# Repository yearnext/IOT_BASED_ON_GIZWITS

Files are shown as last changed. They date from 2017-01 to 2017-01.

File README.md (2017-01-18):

# 智能家居平台介绍
本平台通过机智云+Zigbee来完成智能家居平台的搭建，用户可通过设备控制元件或使用已绑定设备的安卓手机来完成对设备的控制工作。

## 一、模块功能介绍
### 1.1 智能电灯功能介绍
1. 可通过电灯上的按键或APP来控制电灯的开启和关闭。
2. 可通过电灯上的状态指示灯来观察电灯目前的状态。
3. 可通过电灯上的复位按键或者使用APP来还原电灯的出厂数据。
4. 可通过APP来操作电灯进入倒计时运行模式。
5. 可通过APP来操作电灯进入时间段运行模式。
6. 支持断电保持设定数据。
7. 支持设定插座开启的状态。
8. 能够智能判断用户的下一步操作。

### 1.2 智能插座功能介绍
1. 可通过插座上的按键或APP来控制插座的开启和关闭。
2. 可通过插座上的状态指示灯来观察插座目前的状态。
3. 可通过插座上的复位按键或者使用APP来还原插座的出厂数据。
4. 可通过APP来操作插座进入倒计时运行模式。
5. 可通过APP来操作插座进入时间段运行模式。
6. 支持断电保持设定数据。
7. 支持设定插座开启的状态。
8. 能够智能判断用户的下一步操作。

### 1.3 智能窗帘功能介绍
1. 支持手动开启/关闭窗帘。
2. 可通过APP控制窗帘开启/关闭的状态。
3. 可通过APP来操作窗帘进入倒计时运行模式。
4. 可通过APP来操作窗帘进入时间段运行模式。
5. 支持设定窗帘上电时的状态。
6. 支持窗帘下雨警报，可根据用户的配置实现窗帘自动关闭操作。
7. 支持读取室内的亮度数据。
8. 支持断电保持设定数据。
9. 可通过窗帘上的复位按键或者使用APP来还原窗帘的出厂数据。

### 1.4 室内环境监测器功能介绍
1. 能够读取室内的温湿度数据。

## 二、设备通讯协议介绍
### 2.1 数据格式介绍

|通讯类型|事件序号|数据发送/接收方设备类型|数据发送/接收方MAC地址|命令|数据长度|数据|校验和|
|:-:|:-:|:-:|:-:|:-:|:-:|:-:|:-:|
|1 Byte|1 Byte|1 Byte|8 Byte|1 Byte|1 Byte|18 Byte|1 Byte|

#### 2.1.1 通讯类型
|通讯代号|意义|简写|
|:-:|:-:|:-:|
|0x00|结束此次通讯流程|END_COMM|
|0x01|APP请求与设备通讯|W2D|
|0x02|设备应答APP通讯|W2D_ACK|
|0x03|设备请求与APP通讯|D2W|
|0x04|APP应答设备通讯|D2W_ACK|
|0x05|网关请求与设备通讯|H2S|
|0x06|设备应答网关请求|H2S_ACK|
|0x07|设备请求与网关通讯|S2H|
|0x08|网关应答设备请求|S2H_ACK|
|0x09|校验码错误|ERROR_CODE|

#### 2.1.2 事件序号
等待应答的事件序号应与应答的事件序号保持一致。

#### 2.1.3 设备类型
|设备类型|设备代码|
|:-:|:-:|
|网关|0x00|
|APP|0x00|
|灯|0x01|
|插座|0x02|
|窗帘|0x03|
|温湿度传感器|0x04|

**若数据从APP发向设备(W2D、D2W_ACK通讯类型)，设备类型填写数据接收端的设备类型。**

**若数据从设备发向APP(W2D_ACK、D2W通讯类型)，设备类型填写数据发送方的设备类型。**

**若数据从协调器发向终端(H2S、S2H_ACK通讯类型)，设备类型填写数据接收端的设备类型。**

**若数据从终端发向协调器(H2S_ACK、S2H通讯类型)，设备类型填写数据发送方的设备类型。**

#### 2.1.4 设备MAC地址
设备的MAC地址。

**若数据从APP发向设备(W2D、D2W_ACK通讯类型)，设备类型填写数据接收端的MAC地址。**

**若数据从设备发向APP(W2D_ACK、D2W通讯类型)，设备类型填写数据发送方的MAC地址。**

**若数据从协调器发向终端(H2S、S2H_ACK通讯类型)，设备类型填写数据接收端的MAC地址。**

**若数据从终端发向协调器(H2S_ACK、S2H通讯类型)，设备类型填写数据发送方的MAC地址。**

#### 2.1.5 命令
见设备数据点介绍。

#### 2.1.6 数据长度
数据长度表示数据的具体长度，不能超过最大数据长度。

#### 2.1.7 数据
见设备数据点介绍。

#### 2.1.8 校验和
校验和的计算方式为把数据包从通讯类型为开始按字节求和得出的结果对256求余。

### 2.2 设备命令介绍
#### 2.2.1 设备通用基本命令
|控制命令|控制命令介绍|权限|数据点|数据点大小|参数枚举|
|:-:|:-:|:-:|:-:|:-:|:-:|
|0x00|设备心跳命令|只读|-|-|-|
|0x01|恢复设备出厂设备命令|只读|-|-|-|
|0x02|设备重启|只读|-|-|-|
|0x03|刷新设备时间|只读|-|-|-|
|0x04|读取设备时间数据|只读|时间数据|7 Byte|-|
|-|-|-|时间-年数据(21世纪)|1 Byte|0~99|
|-|-|-|时间-月数据|1 Byte|1~12|
|-|-|-|时间-日数据|1 Byte|1~31|
|-|-|-|时间-星期数据|1 Byte|1~7|
|-|-|-|时间-小时数据|1 Byte|0~23|
|-|-|-|时间-分钟数据|1 Byte|0~59|
|-|-|-|时间-秒钟数据|1 Byte|0~59|
|0x05|写入设备时间数据|只写|时间数据|7 Byte|-|
|-|-|-|时间-年数据(21世纪)|1 Byte|0~99|
|-|-|-|时间-月数据|1 Byte|1~12|
|-|-|-|时间-日数据|1 Byte|1~31|
|-|-|-|时间-星期数据|1 Byte|1~7|
|-|-|-|时间-小时数据|1 Byte|0~23|
|-|-|-|时间-分钟数据|1 Byte|0~59|
|-|-|-|时间-秒钟数据|1 Byte|0~59|

#### 2.2.2 网关命令介绍
|控制命令|控制命令介绍|权限|数据点|数据点大小|参数枚举|
|:-:|:-:|:-:|:-:|:-:|:-:|
|0x10|设备列表变化|只读|设备的数量|1 Byte|0~255|
|0x11|APP通过该命令获取目前设备的数量|只读|设备的数量|1 Byte|0~255|
|0x12|APP通过该命令获取目前设备的信息|只读|读取的设备信息|10 Byte|-|
|-|-|-|设备编号（第x台设备）|1 Byte|0 ~ 255|
|-|-|-|设备类型|1 Byte|见设备类型|
|-|-|-|设备MAC地址|8 Byte|见设备MAC地址|
|0x13|设备列表读取失败|只读|-|-|-|

**APP获取设备信息流程介绍**
1. APP向网关设备请求获取在线设备数量。
2. 网关应答APP在线设备数量。
3. APP向网关发送需要获取设备信息的设备编号。
4. 网关回复APP请求的设备编号的设备信息(如果网关返回读取失败命令则APP应该重新执行获取设备信息流程)。
5. APP依次读完所有设备的设备信息。

**注：当设备列表有变化时，设备会向APP发送设备列表变化命令并等待APP读取设备信息。**

#### 2.2.3 电灯命令介绍
|设备命令|设备命令介绍|权限|数据点|数据点大小|参数枚举|
|:-:|:-:|:-:|:-:|:-:|:-:|
|0x10|灯的亮度|只读|Status|1 Byte|0~100(0为关闭，100为开启)|
|0x11|灯的亮度|只写|Status|1 Byte|0~100(0为关闭，100为开启)|
|0x12|定时器单次运行设置|只读|详见定时器数据类型介绍|详见定时器数据类型介绍|详见定时器数据类型介绍|
|0x13|定时器单次运行设置|只写|详见定时器数据类型介绍|详见定时器数据类型介绍|详见定时器数据类型介绍|
|0x14|定时器重复运行设置|只读|详见定时器数据类型介绍|详见定时器数据类型介绍|详见定时器数据类型介绍|
|0x15|定时器重复运行设置|只写|详见定时器数据类型介绍|详见定时器数据类型介绍|详见定时器数据类型介绍|
|0x16|电灯上电运行模式|只读|Mode|1 Byte|0(上电时电灯状态为关闭状态)|
|-|-|-|-|-|1(上电时电灯状态为上一次掉电前的状态)|
|0x17|电灯上电运行模式|只写|Mode|1 Byte|0(上电时电灯状态为关闭状态)|
|-|-|-|-|-|1(上电时电灯状态为上一次掉电前的状态)|

#### 2.2.4 插座命令介绍
|设备命令|设备命令介绍|权限|数据点|数据点大小|参数枚举|
|:-:|:-:|:-:|:-:|:-:|:-:|
|0x10|插座状态|只读|Status|1 Byte|0~1(0为插座关闭，1为插座开启)|
|0x11|插座状态|只写|Status|1 Byte|0~1(0为插座关闭，1为插座开启)|
|0x12|定时器单次运行设置|只读|详见定时器数据类型介绍|详见定时器数据类型介绍|详见定时器数据类型介绍|
|0x13|定时器单次运行设置|只写|详见定时器数据类型介绍|详见定时器数据类型介绍|详见定时器数据类型介绍|
|0x14|定时器重复运行设置|只读|详见定时器数据类型介绍|详见定时器数据类型介绍|详见定时器数据类型介绍|
|0x15|定时器重复运行设置|只写|详见定时器数据类型介绍|详见定时器数据类型介绍|详见定时器数据类型介绍|
|0x16|消耗电能|只读|读取插座消耗的电能|1 Byte|0~100|
|0x17|插座上电运行模式|只读|Mode|1 Byte|0(上电时插座状态为关闭状态)|
|-|-|-|-|-|1(上电时插座状态为上一次掉电前的状态)|
|0x18|插座上电运行模式|只写|Mode|1 Byte|0(上电时插座状态为关闭状态)|
|-|-|-|-|-|1(上电时插座状态为上一次掉电前的状态)|

#### 2.2.5 窗帘命令介绍
|设备命令|设备命令介绍|权限|数据点|数据点大小|参数枚举|
|:-:|:-:|:-:|:-:|:-:|:-:|
|0x10|读取窗帘当前状态|只读|Status|1 Byte|窗帘当前状态|
|-|-|-|-|-|窗帘初始化状态(0x00)|
|-|-|-|-|-|窗帘正在开启状态(0x01)|
|-|-|-|-|-|窗帘完成开启状态(0x02)|
|-|-|-|-|-|窗帘全部开启状态(0x03)|
|-|-|-|-|-|窗帘正在关闭状态(0x04)|
|-|-|-|-|-|窗帘完成关闭状态(0x05)|
|-|-|-|-|-|窗帘全部关闭状态(0x06)|
|0x11|控制窗帘操作命令|只写|Status|1 Byte|窗帘操作命令|
|-|-|-|-|-|打开窗帘(0x01)|
|-|-|-|-|-|合上窗帘(0x02)|
|0x12|定时器单次运行设置|只读|详见定时器数据类型介绍|详见定时器数据类型介绍|详见定时器数据类型介绍|
|0x13|定时器单次运行设置|只写|详见定时器数据类型介绍|详见定时器数据类型介绍|详见定时器数据类型介绍|
|0x14|定时器重复运行设置|只读|详见定时器数据类型介绍|详见定时器数据类型介绍|详见定时器数据类型介绍|
|0x15|定时器重复运行设置|只写|详见定时器数据类型介绍|详见定时器数据类型介绍|详见定时器数据类型介绍|
|0x16|APP通过该命令读取窗帘的工作模式|只读|智能工作模式开关|1 Byte|0~1|
|-|-|-|设定自动关闭窗帘的亮度|1 Byte|0~100|
|0x17|APP通过该命令设置窗帘的工作模式|只写|智能工作模式开关|1 Byte|0~1|
|-|-|-|设定自动关闭窗帘的亮度|1 Byte|0~100|
|0x18|下雨警报|只读|窗帘向APP发送下雨警报|1 Byte|0~1|
|0x19|窗帘检测到的光照前的强度|只读|窗帘向APP发送下雨警报|1 Byte|0~100|
|0x1A|窗帘上电运行模式|只读|窗帘上电运行状态|1 Byte|-|
|-|-|-|-|-|保持现有状态(0x00)|
|-|-|-|-|-|关闭窗帘(0x01)|
|-|-|-|-|-|开启窗帘(0x02)|
|0x1B|窗帘上电运行模式|只写|窗帘上电运行状态|1 Byte|-|
|-|-|-|-|-|保持现有状态(0x00)|
|-|-|-|-|-|关闭窗帘(0x01)|
|-|-|-|-|-|开启窗帘(0x02)|

#### 2.2.6 温湿度传感器命令介绍
|设备命令|设备命令介绍|权限|数据点|数据点大小|参数介绍|
|:-:|:-:|:-:|:-:|:-:|:-:|
|0x10|上报当前环境温湿度数据|只读|上报的温湿度数据|2 Byte|-|
|-|-|-|TEMP|1 Byte|0~100|
|-|-|-|HUMI|1 Byte|0~100|
|0x11|读取当前环境温湿度数据|只读|读取的温湿度数据|2 Byte|-|
|-|-|-|TEMP|1 Byte|0~100|
|-|-|-|HUMI|1 Byte|0~100|

#### 2.2.7 定时器数据格式介绍
|数据名称|成员|成员介绍|权限|占用内存|参数介绍|
|:-:|:-:|:-:|:-:|:-:|:-:|:-:|
|定时器工作模式|-|-|只读|1 Byte|-|
|-|-|-|-|-|TIMER_SLEEP_MODE（定时器休眠模式） = 0x00|
|-|-|-|-|-|TIMER_DOWNCNT_MODE（定时器倒计时运行模式） = 0x01|
|-|-|-|-|-|TIMER_PERIOD_MODE（定时器时间段运行模式） = 0x02|
|-|-|-|-|-|TIMER_CIRCUL_MODE（定时器重复运行模式） = 0x03|
|自定义工作参数|-|-|读/写|1 Byte|配置定时器自定义运行模式的工作参数|
|-|保留|保留|保留|Bit 0(占用该字节的第0位)|0~1|
|-|monday|周一工作状态|读/写|Bit 1(占用该字节的第1位)|0~1|
|-|tuesday|周二工作状态|读/写|Bit 2(占用该字节的第2位)|0~1|
|-|wednesday|周三工作状态|读/写|Bit 3(占用该字节的第3位)|0~1|
|-|thursday|周四工作状态|读/写|Bit 4(占用该字节的第4位)|0~1|
|-|friday|周五工作状态|读/写|Bit 5(占用该字节的第5位)|0~1|
|-|saturday|周六工作状态|读/写|Bit 6(占用该字节的第6位)|0~1|
|-|sunday|周日工作状态|读/写|Bit 7(占用该字节的第7位)|0~1|
|定时器工作时间|-|-|读/写|4 Byte|配置定时器的启动时间和停止时间|
|-|Start_Hour|启动时间-小时|读/写|1 Byte|0~23|
|-|Start_Minute|启动时间-分钟|读/写|1 Byte|0~59|
|-|Stop_Hour|启动时间-小时|读/写|1 Byte|0~23|
|-|Stop_Minute|停止时间-分钟|读/写|1 Byte|0~59|
|设备控制状态|-|-|读/写|2 Byte|配置定时器启动、停止时的设备状态|
|-|device_start_status|设备在定时器启动时的状态|读/写|1 Byte|根据设备而定|
|-|device_end_status|设备在定时器停止时的状态|读/写|1 Byte|根据设备而定|

##### 2.2.7.1 倒计时模式参数配置
例：倒计时8小时35分钟后关闭

    Timer_Mode = TIMER_DOWNCNT_MODE;
    Start_Hour = Now_Time_Hour;
    Start_Minute = Now_Time_Minute;
    Stop_Hour = 8;
    Start_Minute = 35;
    device_start_status = now_status;
    device_end_status = off_status;

**注：**
**1. 当设定定时器工作在倒计时模式时，定时器工作一次，不会重复运行。**
**2. 定时器工作在倒计时模式时不允许出现倒计时时间大于24小时的情况，请注意检查。**

##### 2.2.7.2 时间段模式参数配置
例：8:50~9:45开启

    Timer_Mode = TIMER_SIGNAL_MODE;
    Start_Hour = 8;
    Start_Minute = 50;
    Stop_Hour = 9;
    Start_Minute = 45;
    device_start_status = start_status;
    device_end_status = end_status;

**注：**
**1. 当设定定时器工作在时间段模式时，定时器工作一次，不会重复运行。**
**2. 定时器工作在时间段模式时不允许出现启动时间大于停止时间的情况，请注意检查。**

##### 2.2.7.3 重复运行模式参数配置
例：每周一、周二、周三8:50~9:45开启

    Timer_Mode = TIMER_CUSTOM_MODE;
    monday = 1;
    tuesday = 1;
    wednesday = 1;
    Start_Hour = 8;
    Start_Minute = 50;
    Stop_Hour = 9;
    Start_Minute = 45;
    device_start_status = start_status;
    device_end_status = end_status;

**注：**
**1. 当设定定时器工作在重复运行模式时，定时器会重复运行。**
**2. 定时器工作在重复运行模式时不允许出现启动时间大于停止时间的情况，请注意检查。**

### 2.3 通讯流程介绍
#### 2.3.1 APP控制/读取设备数据流程介绍
APP向设备发送数据流程：

    APP ——> 云端 ——> WIFI模组 ——> 网关 ——> 设备

由上述流程可知APP发送的数据经过云端、WIFI模组、网关处理之后然后才到数据的，中间可能存在一些延迟，因此当APP发送写入/读取设备的数据命令数据经过网关时，网关会将数据发送给终端设备，发送成功的话会发送一个应答数据给云端表示设备正在处理此次事件，而设备解析完APP发送的命令数据之后会将设备信息通过设备上报的形式发送给云端(设备上报数据时的设备命令类型为只读命令)。

设备上报数据流程：

    设备 ——> 网关 ——> WIFI模组 ——> 云端 ——> APP

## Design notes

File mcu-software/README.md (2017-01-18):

# 设备通讯协议介绍
## 一、数据格式介绍

|通讯类型|事件序号|数据发送/接收方设备类型|数据发送/接收方MAC地址|命令|数据长度|数据|校验和|
|:-:|:-:|:-:|:-:|:-:|:-:|:-:|:-:|
|1 Byte|1 Byte|1 Byte|8 Byte|1 Byte|1 Byte|18 Byte|1 Byte|

### 1.1 通讯类型
|通讯代号|意义|简写|
|:-:|:-:|:-:|
|0x00|结束此次通讯流程|END_COMM|
|0x01|APP请求与设备通讯|W2D|
|0x02|设备应答APP通讯|W2D_ACK|
|0x03|设备请求与APP通讯|D2W|
|0x04|APP应答设备通讯|D2W_ACK|
|0x05|网关请求与设备通讯|H2S|
|0x06|设备应答网关请求|H2S_ACK|
|0x07|设备请求与网关通讯|S2H|
|0x08|网关应答设备请求|S2H_ACK|
|0x09|校验码错误|ERROR_CODE|

### 1.2 事件序号
等待应答的事件序号应与应答的事件序号保持一致。

### 1.3 设备类型
|设备类型|设备代码|
|:-:|:-:|
|网关|0x00|
|APP|0x00|
|灯|0x01|
|插座|0x02|
|窗帘|0x03|
|温湿度传感器|0x04|

**若数据从APP发向设备(W2D、D2W_ACK通讯类型)，设备类型填写数据接收端的设备类型。**

**若数据从设备发向APP(W2D_ACK、D2W通讯类型)，设备类型填写数据发送方的设备类型。**

**若数据从协调器发向终端(H2S、S2H_ACK通讯类型)，设备类型填写数据接收端的设备类型。**

**若数据从终端发向协调器(H2S_ACK、S2H通讯类型)，设备类型填写数据发送方的设备类型。**

### 1.4 设备MAC地址
设备的MAC地址。

**若数据从APP发向设备(W2D、D2W_ACK通讯类型)，设备类型填写数据接收端的MAC地址。**

**若数据从设备发向APP(W2D_ACK、D2W通讯类型)，设备类型填写数据发送方的MAC地址。**

**若数据从协调器发向终端(H2S、S2H_ACK通讯类型)，设备类型填写数据接收端的MAC地址。**

**若数据从终端发向协调器(H2S_ACK、S2H通讯类型)，设备类型填写数据发送方的MAC地址。**

### 1.5 命令
见设备数据点介绍。

### 1.6 数据长度
数据长度表示数据的具体长度，不能超过最大数据长度。

### 1.7 数据
见设备数据点介绍。

### 1.8 校验和
校验和的计算方式为把数据包从通讯类型为开始按字节求和得出的结果对256求余。

## 二、设备命令介绍
### 2.1 设备通用基本命令
|控制命令|控制命令介绍|权限|数据点|数据点大小|参数枚举|
|:-:|:-:|:-:|:-:|:-:|:-:|
|0x00|设备心跳命令|只读|-|-|-|
|0x01|恢复设备出厂设备命令|只读|-|-|-|
|0x02|设备重启|只读|-|-|-|
|0x03|刷新设备时间|只读|-|-|-|
|0x04|读取设备时间数据|只读|时间数据|9 Byte|-|
|-|-|-|时间-秒钟数据|1 Byte|0~59|
|-|-|-|时间-分钟数据|1 Byte|0~59|
|-|-|-|时间-小时数据|1 Byte|0~23|
|-|-|-|时间-日数据|1 Byte|1~31|
|-|-|-|时间-月数据|1 Byte|1~12|
|-|-|-|时间-星期数据|1 Byte|1~7|
|-|-|-|时间-年数据|2 Byte|0~65535|
|-|-|-|数据有效位|1 Byte|1:该数据为有效数据|
|-|-|-|-|-|0:该数据为无效数据|
|0x05|写入设备时间数据|只写|时间数据|9 Byte|-|
|-|-|-|时间-秒钟数据|1 Byte|0~59|
|-|-|-|时间-分钟数据|1 Byte|0~59|
|-|-|-|时间-小时数据|1 Byte|0~23|
|-|-|-|时间-日数据|1 Byte|1~31|
|-|-|-|时间-月数据|1 Byte|1~12|
|-|-|-|时间-星期数据|1 Byte|1~7|
|-|-|-|时间-年数据|2 Byte|0~65535|
|-|-|-|数据有效位|1 Byte|1:该数据为有效数据|
|-|-|-|-|-|0:该数据为无效数据|

### 2.2 网关命令介绍
|控制命令|控制命令介绍|权限|数据点|数据点大小|参数枚举|
|:-:|:-:|:-:|:-:|:-:|:-:|
|0x10|设备列表变化|只读|设备的数量|1 Byte|0~255|
|0x11|APP通过该命令获取目前设备的数量|只读|设备的数量|1 Byte|0~255|
|0x12|APP通过该命令获取目前设备的信息|只读|读取的设备信息|10 Byte|-|
|-|-|-|设备编号（第x台设备）|1 Byte|0 ~ 255|
|-|-|-|设备类型|1 Byte|见设备类型|
|-|-|-|设备MAC地址|8 Byte|见设备MAC地址|
|0x13|设备列表读取失败|只读|-|-|-|

**APP获取设备信息流程介绍**
1. APP向网关设备请求获取在线设备数量。
2. 网关应答APP在线设备数量。
3. APP向网关发送需要获取设备信息的设备编号。
4. 网关回复APP请求的设备编号的设备信息(如果网关返回读取失败命令则APP应该重新执行获取设备信息流程)。
5. APP依次读完所有设备的设备信息。

**注：当设备列表有变化时，设备会向APP发送设备列表变化命令并等待APP读取设备信息。**

### 2.3 电灯命令介绍
|设备命令|设备命令介绍|权限|数据点|数据点大小|参数枚举|
|:-:|:-:|:-:|:-:|:-:|:-:|
|0x10|灯的亮度|只读|Status|1 Byte|0~100(0为关闭，100为开启)|
|0x11|灯的亮度|只写|Status|1 Byte|0~100(0为关闭，100为开启)|
|0x12|定时器单次运行设置|只读|详见定时器数据类型介绍|详见定时器数据类型介绍|详见定时器数据类型介绍|
|0x13|定时器单次运行设置|只写|详见定时器数据类型介绍|详见定时器数据类型介绍|详见定时器数据类型介绍|
|0x14|定时器重复运行设置|只读|详见定时器数据类型介绍|详见定时器数据类型介绍|详见定时器数据类型介绍|
|0x15|定时器重复运行设置|只写|详见定时器数据类型介绍|详见定时器数据类型介绍|详见定时器数据类型介绍|
|0x16|电灯上电运行模式|只读|Mode|1 Byte|0(上电时电灯状态为关闭状态)|
|-|-|-|-|-|1(上电时电灯状态为上一次掉电前的状态)|
|0x17|电灯上电运行模式|只写|Mode|1 Byte|0(上电时电灯状态为关闭状态)|
|-|-|-|-|-|1(上电时电灯状态为上一次掉电前的状态)|

### 2.4 插座命令介绍
|设备命令|设备命令介绍|权限|数据点|数据点大小|参数枚举|
|:-:|:-:|:-:|:-:|:-:|:-:|
|0x10|插座状态|只读|Status|1 Byte|0~1(0为插座关闭，1为插座开启)|
|0x11|插座状态|只写|Status|1 Byte|0~1(0为插座关闭，1为插座开启)|
|0x12|定时器单次运行设置|只读|详见定时器数据类型介绍|详见定时器数据类型介绍|详见定时器数据类型介绍|
|0x13|定时器单次运行设置|只写|详见定时器数据类型介绍|详见定时器数据类型介绍|详见定时器数据类型介绍|
|0x14|定时器重复运行设置|只读|详见定时器数据类型介绍|详见定时器数据类型介绍|详见定时器数据类型介绍|
|0x15|定时器重复运行设置|只写|详见定时器数据类型介绍|详见定时器数据类型介绍|详见定时器数据类型介绍|
|0x16|消耗电能|只读|读取插座消耗的电能|1 Byte|0~100|
|0x17|插座上电运行模式|只读|Mode|1 Byte|0(上电时插座状态为关闭状态)|
|-|-|-|-|-|1(上电时插座状态为上一次掉电前的状态)|
|0x18|插座上电运行模式|只写|Mode|1 Byte|0(上电时插座状态为关闭状态)|
|-|-|-|-|-|1(上电时插座状态为上一次掉电前的状态)|

### 2.5 窗帘命令介绍
|设备命令|设备命令介绍|权限|数据点|数据点大小|参数枚举|
|:-:|:-:|:-:|:-:|:-:|:-:|
|0x10|读取窗帘当前状态|只读|Status|1 Byte|窗帘当前状态|
|-|-|-|-|-|窗帘初始化状态(0x00)|
|-|-|-|-|-|窗帘正在开启状态(0x01)|
|-|-|-|-|-|窗帘完成开启状态(0x02)|
|-|-|-|-|-|窗帘全部开启状态(0x03)|
|-|-|-|-|-|窗帘正在关闭状态(0x04)|
|-|-|-|-|-|窗帘完成关闭状态(0x05)|
|-|-|-|-|-|窗帘全部关闭状态(0x06)|
|0x11|控制窗帘操作命令|只写|Status|1 Byte|窗帘操作命令|
|-|-|-|-|-|窗帘动作停止(0x00)|
|-|-|-|-|-|开启窗帘(0x01)|
|-|-|-|-|-|关闭窗帘(0x02)|
|0x12|定时器单次运行设置|只读|详见定时器数据类型介绍|详见定时器数据类型介绍|详见定时器数据类型介绍|
|0x13|定时器单次运行设置|只写|详见定时器数据类型介绍|详见定时器数据类型介绍|详见定时器数据类型介绍|
|0x14|定时器重复运行设置|只读|详见定时器数据类型介绍|详见定时器数据类型介绍|详见定时器数据类型介绍|
|0x15|定时器重复运行设置|只写|详见定时器数据类型介绍|详见定时器数据类型介绍|详见定时器数据类型介绍|
|0x16|APP通过该命令读取窗帘的工作模式|只读|智能工作模式开关|1 Byte|0~1|
|-|-|-|设定自动关闭窗帘的亮度|1 Byte|0~100|
|0x17|APP通过该命令设置窗帘的工作模式|只写|智能工作模式开关|1 Byte|0~1|
|-|-|-|设定自动关闭窗帘的亮度|1 Byte|0~100|
|0x18|下雨警报|只读|窗帘向APP发送下雨警报|1 Byte|0~1|
|0x19|窗帘检测到的光照前的强度|只读|窗帘检测到的亮度信息|1 Byte|0~100|
|0x1A|窗帘上电运行模式|只读|窗帘上电运行状态|1 Byte|-|
|-|-|-|-|-|保持现有状态(0x00)|
|-|-|-|-|-|关闭窗帘(0x01)|
|-|-|-|-|-|开启窗帘(0x02)|
|0x1B|窗帘上电运行模式|只写|窗帘上电运行状态|1 Byte|-|
|-|-|-|-|-|保持现有状态(0x00)|
|-|-|-|-|-|关闭窗帘(0x01)|
|-|-|-|-|-|开启窗帘(0x02)|

### 2.6 温湿度传感器命令介绍
|设备命令|设备命令介绍|权限|数据点|数据点大小|参数介绍|
|:-:|:-:|:-:|:-:|:-:|:-:|
|0x10|上报当前环境温湿度数据|只读|上报的温湿度数据|2 Byte|-|
|-|-|-|TEMP|1 Byte|0~50|
|-|-|-|HUMI|1 Byte|0~100|
|0x11|读取当前环境温湿度数据|只读|读取的温湿度数据|2 Byte|-|
|-|-|-|TEMP|1 Byte|0~50|
|-|-|-|HUMI|1 Byte|0~100|
注：由于温湿度传感器精度问题，只能检测到0~50摄氏度的温度且温度误差在正负2摄氏度内，检测到的湿度范围为20%~90%，且湿度误差在正负5%范围内。

### 2.7 定时器数据格式介绍
|数据名称|成员|成员介绍|权限|占用内存|参数介绍|
|:-:|:-:|:-:|:-:|:-:|:-:|:-:|
|定时器工作模式|-|-|只读|1 Byte|-|
|-|-|-|-|-|TIMER_SLEEP_MODE（定时器休眠模式） = 0x00|
|-|-|-|-|-|TIMER_DOWNCNT_MODE（定时器倒计时运行模式） = 0x01|
|-|-|-|-|-|TIMER_PERIOD_MODE（定时器时间段运行模式） = 0x02|
|-|-|-|-|-|TIMER_CIRCUL_MODE（定时器重复运行模式） = 0x03|
|自定义工作参数|-|-|读/写|1 Byte|配置定时器自定义运行模式的工作参数|
|-|保留|保留|保留|Bit 0(占用该字节的第0位)|0~1|
|-|monday|周一工作状态|读/写|Bit 1(占用该字节的第1位)|0~1|
|-|tuesday|周二工作状态|读/写|Bit 2(占用该字节的第2位)|0~1|
|-|wednesday|周三工作状态|读/写|Bit 3(占用该字节的第3位)|0~1|
|-|thursday|周四工作状态|读/写|Bit 4(占用该字节的第4位)|0~1|
|-|friday|周五工作状态|读/写|Bit 5(占用该字节的第5位)|0~1|
|-|saturday|周六工作状态|读/写|Bit 6(占用该字节的第6位)|0~1|
|-|sunday|周日工作状态|读/写|Bit 7(占用该字节的第7位)|0~1|
|定时器工作时间|-|-|读/写|4 Byte|配置定时器的启动时间和停止时间|
|-|Start_Hour|启动时间-小时|读/写|1 Byte|0~23|
|-|Start_Minute|启动时间-分钟|读/写|1 Byte|0~59|
|-|Stop_Hour|启动时间-小时|读/写|1 Byte|0~23|
|-|Stop_Minute|停止时间-分钟|读/写|1 Byte|0~59|
|设备控制状态|-|-|读/写|2 Byte|配置定时器启动、停止时的设备状态|
|-|device_start_status|设备在定时器启动时的状态|读/写|1 Byte|根据设备而定|
|-|device_end_status|设备在定时器停止时的状态|读/写|1 Byte|根据设备而定|

#### 2.7.1 倒计时模式参数配置
例：倒计时8小时35分钟后关闭

    Timer_Mode = TIMER_DOWNCNT_MODE;
    Start_Hour = Now_Time_Hour;
    Start_Minute = Now_Time_Minute;
    Stop_Hour = 8;
    Start_Minute = 35;
    device_start_status = now_status;
    device_end_status = off_status;

**注：**
**1. 当设定定时器工作在倒计时模式时，定时器工作一次，不会重复运行。**
**2. 定时器工作在倒计时模式时不允许出现倒计时时间大于24小时的情况，请注意检查。**

#### 2.7.2 时间段模式参数配置
例：8:50~9:45开启

    Timer_Mode = TIMER_SIGNAL_MODE;
    Start_Hour = 8;
    Start_Minute = 50;
    Stop_Hour = 9;
    Start_Minute = 45;
    device_start_status = start_status;
    device_end_status = end_status;

**注：**
**1. 当设定定时器工作在时间段模式时，定时器工作一次，不会重复运行。**
**2. 定时器工作在时间段模式时不允许出现启动时间大于停止时间的情况，请注意检查。**

#### 2.7.3 重复运行模式参数配置
例：每周一、周二、周三8:50~9:45开启

    Timer_Mode = TIMER_CUSTOM_MODE;
    monday = 1;
    tuesday = 1;
    wednesday = 1;
    Start_Hour = 8;
    Start_Minute = 50;
    Stop_Hour = 9;
    Start_Minute = 45;
    device_start_status = start_status;
    device_end_status = end_status;

**注：**
**1. 当设定定时器工作在重复运行模式时，定时器会重复运行。**
**2. 定时器工作在重复运行模式时不允许出现启动时间大于停止时间的情况，请注意检查。**
>>>>>>> ec588fe... 修复了温湿度数据读取失败的BUG

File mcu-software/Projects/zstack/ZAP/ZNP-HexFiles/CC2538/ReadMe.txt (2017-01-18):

When using ZNP hex images, the host processor must register for specific ZDO
callbacks of interest using the ZDO_MSG_CB_REGISTER API, and will be notified
of the response via the ZDO_MSG_CB_INCOMING command. The ZAP applications
incuded with this release demonstrate this method of handling ZDO responses.

For use with SPI serial interface -
 CC2538ZNP-SPI-Pro.hex -
  To be used with ZNP applications that do not use security.

 CC2538ZNP-SPI-Pro-Secure_Standard.hex -
  To be used with ZNP applications that use standard ZigBee security joining
  where the NWK key is sent in the clear or is pre-configured.

 CC2538ZNP-SPI-Pro-Secure_LinkKeyJoin.hex -
  To be used with ZNP applications that use the Pre-configured Trust Center
  Link Key method of joining where the pre-configured trust center link key
  is used to encrypt the APS tunnel command which contains the NWK key.

For use with UART serial interface -
 CC2538ZNP-UART-Pro.hex -
  To be used with ZNP applications that do not use security.

 CC2538ZNP-UART-Pro-Secure_Standard.hex -
  To be used with ZNP applications that use standard ZigBee security joining
  where the NWK key is sent in the clear or is pre-configured.

 CC2538ZNP-UART-Pro-Secure_LinkKeyJoin.hex -
  To be used with ZNP applications that use the Pre-configured Trust Center
  Link Key method of joining where the pre-configured trust center link key
  is used to encrypt the APS tunnel command which contains the NWK key.

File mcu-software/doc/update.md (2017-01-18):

# IOT_BASE_ON_GIZWITS更新日志——mcu_software_debug分支
## 一、更新日志
**固件版本：IOTBaseOnGizwits_MCUSoftwareDebug_0.2.17_alpha_201612282310**
+ 添加检测到新设备就向APP发送请求更新设备列表命令(待测试)。

**固件版本：IOTBaseOnGizwits_MCUSoftwareDebug_0.2.16_alpha_201612271448**
+ 修改网络时间推送策略，改为网关获取到时间更新主动推送给其他设备，设备会在30s内主动获取网络时间。
+ 添加发送广播程序。
+ 添加写入设备时间命令的解析。

**固件版本：IOTBaseOnGizwits_MCUSoftwareDebug_0.2.15_alpha_201612261700**
+ 添加网关获取网络事时间前置标志。

**固件版本：IOTBaseOnGizwits_MCUSoftwareDebug_0.2.14_alpha_201612261423**
+ 修改窗帘速度检测时间。

**固件版本：IOTBaseOnGizwits_MCUSoftwareDebug_0.2.13_alpha_201612252343**
+ 切换电灯控制按键为电容按键。

**固件版本：IOTBaseOnGizwits_MCUSoftwareDebug_0.2.12_alpha_201612252330**
+ 修复了窗帘定时器回调存在递归的BUG。
+ 修改通讯协议标注错误的问题。

**固件版本：IOTBaseOnGizwits_MCUSoftwareDebug_0.2.11_alpha_201612242230**
+ 修复了定时器运行错误的BUG。
+ 修复了网关获取网络时间过长的BUG。
+ 修改网关清除僵尸设备的时间。
+ 延长设备心跳时间。
+ 添加定时器操作设备的状态上报操作。
+ 修复的下雨状态检测不正常的BUG。
+ 修复通讯协议部分内容。
+ 添加电灯设备的路由分支。
+ 解决了定时器无法在启动后立即停止设备的BUG。

**固件版本：IOTBaseOnGizwits_MCUSoftwareDebug_0.2.10_alpha_201612240022**
+ 修复了电动窗帘上电自动运行的BUG。
+ 修复了电动窗帘按键失灵的BUG。
+ 修复了按键过于灵敏的BUG。

**固件版本：IOTBaseOnGizwits_MCUSoftwareDebug_0.2.9_alpha_201612212337**
+ 完成ZSTACK的NV操作调试。
+ 添加更新日志。
+ 添加设备时钟芯片使能/禁用开关。
+ 添加设备数据保存使能/禁用开关。
+ 修改电灯默认上电状态为关闭状态。
+ 解决了电动窗帘无法实现远程和按键连续控制的BUG。

**固件版本：IOTBaseOnGizwits_MCUSoftwareDebug_0.2.8_alpha_201612201138**
+ 修复倒计时定时器不能正常工作的BUG。

**固件版本：IOTBaseOnGizwits_MCUSoftwareDebug_0.2.7_alpha_201612192312**
+ 修复设备从网关获取时间不正确的BUG。
+ 修复了读取设备列表不正确的BUG。
+ 禁用除COORD设备的串口2驱动。
+ 修改工程清理的批处理文件。
+ 修复设备无法上报消息的BUG。

**固件版本：IOTBaseOnGizwits_MCUSoftwareDebug_0.2.6_alpha_201612181939**
+ 进入DEBUG阶段。

**固件版本：IOTBaseOnGizwits_MCUSoftwareDebug_0.2.5_alpha_201612172346**
+ 解决电动窗帘电机运行时单片机死机的BUG。

**固件版本：IOTBaseOnGizwits_MCUSoftwareDebug_0.2.4_alpha_201612162350**
+ 发现BUG：电动窗帘电机运行时单片机死机。

**固件版本：IOTBaseOnGizwits_MCUSoftwareDebug_0.2.3_alpha_201612142327**
+ 修复zigbee设备底层通讯错误的BUG。
+ 准备进入DEBUG阶段。

**固件版本：IOTBaseOnGizwits_MCUSoftwareDebug_0.2.2_alpha_201612132303**
+ 重写设备列表服务。
+ 分离COORD组件。
+ 增加COORD设备控制程序。
+ 修改空应答机制。
+ 解决抓包失败导致接收缓冲区错误的BUG。
+ 发现：按键反应迟钝BUG。
+ 提高通讯稳定性。

**固件版本：IOTBaseOnGizwits_MCUSoftwareDebug_0.2.1_alpha_201612121622**
+ 修改设备类型判断代码。
+ 使用标准库进行结构体偏移量的计算。
+ 新建工程模版。

**固件版本：IOTBaseOnGizwits_MCUSoftwareDebug_0.2.0_alpha_201612102211**
+ 重写MYPROTOCOL程序框架。

**固件版本：IOTBaseOnGizwits_MCUSoftwareDebug_0.1.27_alpha_201612072222**
+ 修复温湿度数据读取错误的BUG。
+ 降低温湿度数据的读取时间。

**固件版本：IOTBaseOnGizwits_MCUSoftwareDebug_0.1.26_alpha_201612062254**
+ 添加智能插座初始化程序。
+ 修改工程目录结构。

**固件版本：IOTBaseOnGizwits_MCUSoftwareDebug_0.1.25_alpha_201612022237**
+ 添加自动校时服务。

**固件版本：IOTBaseOnGizwits_MCUSoftwareDebug_0.1.24_alpha_201611282112**
+ 添加电动窗帘应答服务。

**固件版本：IOTBaseOnGizwits_MCUSoftwareDebug_0.1.23_alpha_201611271452**
+ 修改电动窗帘模块功能，添加对环境亮度的检测。

**固件版本：IOTBaseOnGizwits_MCUSoftwareDebug_0.1.22_alpha_201611252216**
+ 添加ADC转换程序。
+ 修改定时器组件。

**固件版本：IOTBaseOnGizwits_MCUSoftwareDebug_0.1.21_alpha_201611242229**
+ 修改硬件电路。
+ 完善电动窗帘的硬件抽象层。
+ 修改DS1302驱动程序。

**固件版本：IOTBaseOnGizwits_MCUSoftwareDebug_0.1.20_alpha_201611222241**
+ 修改数据存储服务。

**固件版本：IOTBaseOnGizwits_MCUSoftwareDebug_0.1.19_alpha_201611212228**
+ 修改硬件IO配置。
+ 修改电动窗帘的按键检测处理策略。
+ 修改MYPROTOCOL底层通讯程序。
+ 增加帮助文档。
+ 添加星期计算程序。
+ 完善获取网络时间服务。

**固件版本：IOTBaseOnGizwits_MCUSoftwareDebug_0.1.18_alpha_201611202354**
+ 整合硬件资源。
+ 完善MYPROTOCOL框架。
+ 添加电动窗帘的处理程序。

**固件版本：IOTBaseOnGizwits_MCUSoftwareDebug_0.1.17_alpha_201611042210**
+ 修改网关回复APP请求控制设备应答处理。

**固件版本：IOTBaseOnGizwits_MCUSoftwareDebug_0.1.16_alpha_201611032241**
+ 修复了网关未连接APP却仍然向APP发送命令请求BUG。

**固件版本：IOTBaseOnGizwits_MCUSoftwareDebug_0.1.15_alpha_201611022235**
+ 添加对温湿度传感器设备的处理程序。
+ 添加对智能插座设备的处理程序。
+ 修改温湿度传感器设备的控制命令。

**固件版本：IOTBaseOnGizwits_MCUSoftwareDebug_0.1.14_alpha_201610311910**
+ 更新通讯协议定时器章节的说明。
+ 修改定时器处理程序。
+ 定时器程序支持通讯协议标准。

**固件版本：IOTBaseOnGizwits_MCUSoftwareDebug_0.1.13_alpha_201610302259**
+ 修复组网状态指示灯显示异常的BUG。
+ 修改通讯协议定时器章节说明。
+ 修改通讯协议介绍。

**固件版本：IOTBaseOnGizwits_MCUSoftwareDebug_0.1.12_alpha_201610292001**
+ 修复了添加设备失败的BUG。
+ 修改MYPROTOCOL的日志打印配置。

**固件版本：IOTBaseOnGizwits_MCUSoftwareDebug_0.1.11_alpha_201610282359**
+ 禁用MYPROTOCOL框架的数据发送缓冲机制。
+ 修改发包函数。
+ 解决主机无法接收到从机发送的数据的BUG。
+ 修改USE_GIZWITS_MOD宏为MYPROTOCOL_DEVICE_COORD宏。

**固件版本：IOTBaseOnGizwits_MCUSoftwareDebug_0.1.10_alpha_201610272246**
+ 修改设备状态变化处理策略。
+ 修改通讯协议通讯类型注释内容。
+ 修改通讯协议定时器模块注释内容。
+ 优化数据包解析框架。
+ 修正底层通讯程序发送目标设设置不正确的BUG。
+ 整合MYPROTOCOL模块。
+ 已知BUG：主机无法接收到从机发送的数据。

**固件版本：IOTBaseOnGizwits_MCUSoftwareDebug_0.1.9_alpha_201610252302**
+ 修改按键检测处理策略。

**固件版本：IOTBaseOnGizwits_MCUSoftwareDebug_0.1.8_alpha_201610241122**
+ 添加智能电灯定时器后台服务。
+ 修复了DS1302数据读写错误的BUG。
+ 修复了DHT11读取数据时校验和计算错误的BUG。

**固件版本：IOTBaseOnGizwits_MCUSoftwareDebug_0.1.7_alpha_201610222328**
+ 修改部分通讯协议内容，增加通讯流程说明。
+ 完成智能电灯的开发工作，进入DEBUG阶段。
+ 添加机智云固件初始化程序。
+ 已知问题：终端设备无法加入网络。

**固件版本：IOTBaseOnGizwits_MCUSoftwareDebug_0.1.6_alpha_201610211726**
+ 修改设备通讯类型。
+ 修改底层通讯程序。

**固件版本：IOTBaseOnGizwits_MCUSoftwareDebug_0.1.5_alpha_201610202301**
+ 添加自动检测设备类型代码。
+ 完善通讯协议的介绍。

**固件版本：IOTBaseOnGizwits_MCUSoftwareDebug_0.1.4_alpha_201610191105**
+ 修改通讯协议定时器部分内容
+ 添加定时器任务的处理程序。

**固件版本：IOTBaseOnGizwits_MCUSoftwareDebug_0.1.3_alpha_201610181027**
+ 修改应用定时器的结构。

**固件版本：IOTBaseOnGizwits_MCUSoftwareDebug_0.1.2_alpha_201610171858**
+ 完成应用定时器工作状态检测。
+ 整合通讯协议。

**固件版本：IOTBaseOnGizwits_MCUSoftwareDebug_0.1.1_alpha_201610161038**
+ 整合数据包发送程序。

**固件版本：IOTBaseOnGizwits_MCUSoftwareDebug_0.1.0_alpha_201610150748**
+ 修改程序框架，整合各个资源模块进行集中控制。

**固件版本：IOTBaseOnGizwits_MCUSoftwareDebug_0.0.13_alpha_201610141627**
+ 添加按键检测程序。
+ 禁用ZSTACK自带的定时器驱动程序。
+ 完成CC2530的FLASH测试。
+ 修改定时器驱动。

**固件版本：IOTBaseOnGizwits_MCUSoftwareDebug_0.0.12_alpha_201610131528**
+ 完成呼吸灯的测试。

**固件版本：IOTBaseOnGizwits_MCUSoftwareDebug_0.0.11_alpha_201610122228**
+ 添加定时器PWM驱动程序。

**固件版本：IOTBaseOnGizwits_MCUSoftwareDebug_0.0.10_alpha_201610110946**
+ 禁用ZSTACK自带的LED驱动和KEY驱动程序。
+ 设备心跳通讯测试成功。

**固件版本：IOTBaseOnGizwits_MCUSoftwareDebug_0.0.9_alpha_201610101634**
+ 修复了终端设备串口波特率调整不当的BUG。

**固件版本：IOTBaseOnGizwits_MCUSoftwareDebug_0.0.8_alpha_201610092303**
+ 添加获取网络时间数据包。
+ 数据包解析框架开发中。

**固件版本：IOTBaseOnGizwits_MCUSoftwareDebug_0.0.7_alpha_201610051154**
+ 完成Gizwits通讯与Zigbee之间的兼容测试。

**固件版本：IOTBaseOnGizwits_MCUSoftwareDebug_0.0.6_alpha_201610040803**
+ 添加错误数据包的处理机制。
+ 添加结束通讯机制。

**固件版本：IOTBaseOnGizwits_MCUSoftwareDebug_0.0.5_alpha_201610031635**
+ 完成CC2530网关和ESP8266通讯。

**固件版本：IOTBaseOnGizwits_MCUSoftwareDebug_0.0.4_alpha_201609291115**
+ 更新工程文件，未解决UART1工作异常的问题。

**固件版本：IOTBaseOnGizwits_MCUSoftwareDebug_0.0.3_alpha_201609282133**
+ 开启ZSTACK的双串口，已知问题为UART1无法正常工作。

**固件版本：IOTBaseOnGizwits_MCUSoftwareDebug_0.0.2_alpha_201609280955**
+ 完成机智云固件的移植工作。

**固件版本：IOTBaseOnGizwits_MCUSoftwareDebug_0.0.1_alpha_201609271352**
+ 新建工程，启动项目开发。
+ 实现Zigbee设备的P2P通讯。

## 2、版本命名规则
### 2.1 版本信息格式介绍
工程名\_分支名\_主版本号.子版本号.修正版本号\_版本类型\_编译时间
示例：IOTBaseOnGizwits_MCUSoftwareDebug_0.0.1_alpha_201609271352

|格式名称|参数介绍|
|:-:|:-:|
|工程名|IOTBaseOnGizwits|
|分支名|MCUSoftwareDebug|
|主版本号|0|
|子版本号|0|
|修正版本号|1|
|版本类型|alpha|
|编译时间|201609271352|

### 2.2 版本号管理策略
+ 项目初版本时，版本号可以为 0.1 或 0.1.0, 也可以为 1.0 或 1.0.0。
+ 当项目在进行了局部修改或 bug 修正时，主版本号和子版本号都不变，修正版本号加1。
+ 当项目在原有的基础上增加了部分功能时，主版本号不变，子版本号加1，修正版本号复位为0，因而可以被忽略掉
+ 当项目在进行了重大修改或局部修正累积较多，而导致项目整体发生全局变化时，主版本号加1。

### 2.3 版本类型介绍

|版本类型|版本名称|版本介绍|
|:-:|:-:|:-:|
|测试版本|-|-|
|-|Alphal|内部测试版|
|-|Beta|外部测试版|
|-|M 版|Milestone， 每个开发阶段的终结点的里程碑版本|
|-|Trail|试用版（含有某些限制，如时间、功能，注册后也有可能变为正式版）|
|-|RC版|Release Candidate，意思是发布倒计时，该版本已经完成全部功能并清除大部分的BUG。到了这个阶段只会除BUG，不会对软件做任何大的更改|
|-|RTM版|Release To Manufactur，意思是发布到生产商，这基本就是最终的版本|
|-|GA版|Generally Available，最终版|
|正式版本|-|-|
|-|Enhance|增强版或者加强版|
|-|Full version|完全版|
|-|Release|发行版，有时间限制|
|-|Upgrade|升级版|
|-|Retail|零售版|
|-|Plus|增强版，不过这种大部分是在程序界面及多媒体功能上增强|

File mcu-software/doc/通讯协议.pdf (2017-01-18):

# 设备通讯协议介绍

# 一、数据格式介绍

通讯类型 | 事件序号 | 数据发送/接收方设备类型 | 数据发送/接收方MAC地址 | 命令 | 数据长度 | 数据 | 校验和
1 Byte | 1 Byte | 1 Byte | 8 Byte | 1 Byte | 1 Byte | 18 Byte | 1 Byte

## 1.1 通讯类型

通讯代号 | 意义 | 简写
0x00 | 结束此次通讯流程 | END_COMM
0x01 | APP请求与设备通讯 | W2D
0x02 | 设备应答APP通讯 | W2D_ACK
0x03 | 设备请求与APP通讯 | D2W
0x04 | APP应答设备通讯 | D2W_ACK
0x05 | 网关请求与设备通讯 | H2S
0x06 | 设备应答网关请求 | H2S_ACK
0x07 | 设备请求与网关通讯 | S2H
0x08 | 网关应答设备请求 | S2H_ACK
0x09 | 校验码错误 | ERROR_CODE

## 1.2 事件序号

等待应答的事件序号应与应答的事件序号保持一致。

## 1.3 设备类型

设备类型 | 设备代码
网关 | 0x00
APP | 0x00
灯 | 0x01
插座 | 0x02
窗帘 | 0x03
温湿度传感器 | 0x04

若数据从APP发向设备(W2D、D2W_ACK通讯类型)，设备类型填写数据接收端的设备类型。

若数据从设备发向APP(W2D_ACK、D2W通讯类型)，设备类型填写数据发送方的设备类型。

若数据从协调器发向终端(H2S、S2H_ACK通讯类型)，设备类型填写数据接收端的设备类型。

若数据从终端发向协调器(H2S_ACK、S2H通讯类型)，设备类型填写数据发送方的设备类型。

### 1.4 设备MAC地址

设备的MAC地址。

若数据从APP发向设备(W2D、D2W_ACK通讯类型)，设备类型填写数据接收端的MAC地址。

若数据从设备发向APP(W2D_ACK、D2W通讯类型)，设备类型填写数据发送方的MAC地址。

若数据从协调器发向终端(H2S、S2H_ACK通讯类型)，设备类型填写数据接收端的MAC地址。

若数据从终端发向协调器(H2S_ACK、S2H通讯类型)，设备类型填写数据发送方的MAC地址。

### 1.5 命令

见设备数据点介绍。

## 1.6 数据长度

数据长度表示数据的具体长度，不能超过最大数据长度。

### 1.7 数据

见设备数据点介绍。

### 1.8 校验和

校验和的计算方式为把数据包从通讯类型为开始按字节求和得出的结果对256求余。

# 二、设备命令介绍

## 2.1 设备通用基本命令

控制命令 | 控制命令介绍 | 权限 | 数据点 | 数据点大小 | 参数枚举
0x00 | 设备心跳命令 | 只读 | - | - | -
0x01 | 恢复设备出厂设备命令 | 只读 | - | - | -
0x02 | 设备重启 | 只读 | - | - | -
0x03 | 刷新设备时间 | 只读 | - | - | -
0x04 | 读取设备时间数据 | 只读 | 时间数据 | 9 Byte | -
- | - | - | 时间-秒钟数据 | 1 Byte | 0~59
- | - | - | 时间-分钟数据 | 1 Byte | 0~59
- | - | - | 时间-小时数据 | 1 Byte | 0~23
- | - | - | 时间-日数据 | 1 Byte | 1~31
- | - | - | 时间-月数据 | 1 Byte | 1~12
- | - | - | 时间-星期数据 | 1 Byte | 1~7
- | - | - | 时间-年数据 | 2 Byte | 0~65535
- | - | - | 数据有效位 | 1 Byte | 1:该数据为有效数据
- | - | - | - | - | 0:该数据为无效数据
0x05 | 写入设备时间数据 | 只写 | 时间数据 | 9 Byte | -

- | - | - | 时间-秒钟数据 | 1 Byte | 0~59
- | - | - | 时间-分钟数据 | 1 Byte | 0~59
- | - | - | 时间-小时数据 | 1 Byte | 0~23
- | - | - | 时间-日数据 | 1 Byte | 1~31
- | - | - | 时间-月数据 | 1 Byte | 1~12
- | - | - | 时间-星期数据 | 1 Byte | 1~7
- | - | - | 时间-年数据 | 2 Byte | 0~65535
- | - | - | 数据有效位 | 1 Byte | 1:该数据为有效数据
- | - | - | - | - | 0:该数据为无效数据

## 2.2 网关命令介绍

控制命令 | 控制命令介绍 | 权限 | 数据点 | 数据点大小 | 参数枚举
0x10 | 设备列表变化 | 只读 | 设备的数量 | 1 Byte | 0~255
0x11 | APP通过该命令获取目前设备的数量 | 只读 | 设备的数量 | 1 Byte | 0~255
0x12 | APP通过该命令获取目前设备的信息 | 只读 | 读取的设备信息 | 10 Byte | -
- | - | - | 设备编号（第x台设备） | 1 Byte | 0 ~ 255
- | - | - | 设备类型 | 1 Byte | 见设备类型
- | - | - | 设备MAC地址 | 8 Byte | 见设备MAC地址
0x13 | 设备列表读取失败 | 只读 | - | - | -

APP获取设备信息流程介绍

1. APP向网关设备请求获取在线设备数量。
2. 网关应答APP在线设备数量。
3. APP向网关发送需要获取设备信息的设备编号。
4. 网关回复APP请求的设备编号的设备信息(如果网关返回读取失败命令则APP应该重新执行获取设备信息流程)。
5. APP依次读完所有设备的设备信息。

注：当设备列表有变化时，设备会向APP发送设备列表变化命令并等待APP读取设备信息。

## 2.3 电灯命令介绍

设备命
令

设备命令介绍

权
限
数据点 | 数据点大小 | 参数枚举
0x10 | 灯的亮度 | 只 读 | Status | 1 Byte | 0~100(0为关闭，100为开启)
0x11 | 灯的亮度 | 只 写 | Status | 1 Byte | 0~100(0为关闭，100为开启)
0x12 | 定时器单次运行设 置 | 只 读 | 详见定时器数据类型介 绍 | 详见定时器数据类型介 绍 | 详见定时器数据类型介绍
0x13 | 定时器单次运行设 置 | 只 写 | 详见定时器数据类型介 绍 | 详见定时器数据类型介 绍 | 详见定时器数据类型介绍

0x14 | 定时器重复运行设 置 | 只 读 | 详见定时器数据类型介 绍 | 详见定时器数据类型介 绍 | 详见定时器数据类型介绍
0x15 | 定时器重复运行设 置 | 只 写 | 详见定时器数据类型介 绍 | 详见定时器数据类型介 绍 | 详见定时器数据类型介绍
0x16 | 电灯上电运行模式 | 只 读 | Mode | 1 Byte | 0(上电时电灯状态为关闭状态)
- | - | - | - | - | 1(上电时电灯状态为上一次掉电前的状 态)
0x17 | 电灯上电运行模式 | 只 写 | Mode | 1 Byte | 0(上电时电灯状态为关闭状态)
- | - | - | - | - | 1(上电时电灯状态为上一次掉电前的状 态)

## 2.4 插座命令介绍

设备命 令 | 设备命令介绍 | 权 限 | 数据点 | 数据点大小 | 参数枚举
0x10 | 插座状态 | 只 读 | Status | 1 Byte | 0~1(0为插座关闭，1为插座开启)
0x11 | 插座状态 | 只 写 | Status | 1 Byte | 0~1(0为插座关闭，1为插座开启)
0x12 | 定时器单次运行设 置 | 只 读 | 详见定时器数据类型介 绍 | 详见定时器数据类型介 绍 | 详见定时器数据类型介绍
0x13 | 定时器单次运行设 置 | 只 写 | 详见定时器数据类型介 绍 | 详见定时器数据类型介 绍 | 详见定时器数据类型介绍
0x14 | 定时器重复运行设 置 | 只 读 | 详见定时器数据类型介 绍 | 详见定时器数据类型介 绍 | 详见定时器数据类型介绍
0x15 | 定时器重复运行设 置 | 只 写 | 详见定时器数据类型介 绍 | 详见定时器数据类型介 绍 | 详见定时器数据类型介绍
0x16 | 消耗电能 | 只 读 | 读取插座消耗的电能 | 1 Byte | 0~100
0x17 | 插座上电运行模式 | 只 读 | Mode | 1 Byte | 0(上电时插座状态为关闭状态)
- | - | - | - | - | 1(上电时插座状态为上一次掉电前的状 态)
0x18 | 插座上电运行模式 | 只 写 | Mode | 1 Byte | 0(上电时插座状态为关闭状态)
- | - | - | - | - | 1(上电时插座状态为上一次掉电前的状 态)

## 2.5 窗帘命令介绍

设备命; 设备命令介绍; 数据点; 数据点大小; 参数枚举

0x10 | 读取窗帘当前状态 | 只 读 | Status | 1 Byte | 窗帘当前状态
- | - | - | - | - | 窗帘初始化状态(0x00)
- | - | - | - | - | 窗帘正在开启状态 (0x01)
- | - | - | - | - | 窗帘完成开启状态 (0x02)
- | - | - | - | - | 窗帘全部开启状态 (0x03)
- | - | - | - | - | 窗帘正在关闭状态 (0x04)
- | - | - | - | - | 窗帘完成关闭状态 (0x05)
- | - | - | - | - | 窗帘全部关闭状态 (0x06)
0x11 | 控制窗帘操作命令 | 只 写 | Status | 1 Byte | 窗帘操作命令
- | - | - | - | - | 窗帘动作停止(0x00)
- | - | - | - | - | 开启窗帘(0x01)
- | - | - | - | - | 关闭窗帘(0x02)
0x12 | 定时器单次运行设置 | 只 读 | 详见定时器数据类型介 绍 | 详见定时器数据类型介 绍 | 详见定时器数据类型介 绍
0x13 | 定时器单次运行设置 | 只 写 | 详见定时器数据类型介 绍 | 详见定时器数据类型介 绍 | 详见定时器数据类型介 绍
0x14 | 定时器重复运行设置 | 只 读 | 详见定时器数据类型介 绍 | 详见定时器数据类型介 绍 | 详见定时器数据类型介 绍
0x15 | 定时器重复运行设置 | 只 写 | 详见定时器数据类型介 绍 | 详见定时器数据类型介 绍 | 详见定时器数据类型介 绍
0x16 | APP通过该命令读取窗帘的工作模 式 | 只 读 | 智能工作模式开关 | 1 Byte | 0~1
- | - | - | 设定自动关闭窗帘的亮 度 | 1 Byte | 0~100
0x17 | APP通过该命令设置窗帘的工作模 式 | 只 写 | 智能工作模式开关 | 1 Byte | 0~1
- | - | - | 设定自动关闭窗帘的亮 度 | 1 Byte | 0~100
0x18 | 下雨警报 | 只 读 | 窗帘向APP发送下雨警 报 | 1 Byte | 0~1
0x19 | 窗帘检测到的光照前的强度 | 只 读 | 窗帘检测到的亮度信息 | 1 Byte | 0~100
0x1A | 窗帘上电运行模式 | 只 读 | 窗帘上电运行状态 | 1 Byte | -

- | - | - | - | - | 保持现有状态(0x00)
- | - | - | - | - | 关闭窗帘(0x01)
- | - | - | - | - | 开启窗帘(0x02)
0x1B | 窗帘上电运行模式 | 只 写 | 窗帘上电运行状态 | 1 Byte | -
- | - | - | - | - | 保持现有状态(0x00)
- | - | - | - | - | 关闭窗帘(0x01)
- | - | - | - | - | 开启窗帘(0x02)

## 2.6 温湿度传感器命令介绍

设备命令 | 设备命令介绍 | 权限 | 数据点 | 数据点大小 | 参数介绍
0x10 | 上报当前环境温湿度数据 | 只读 | 上报的温湿度数据 | 2 Byte | -
- | - | - | TEMP | 1 Byte | 0~50
- | - | - | HUMI | 1 Byte | 0~100
0x11 | 读取当前环境温湿度数据 | 只读 | 读取的温湿度数据 | 2 Byte | -
- | - | - | TEMP | 1 Byte | 0~50
- | - | - | HUMI | 1 Byte | 0~100

注：由于温湿度传感器精度问题，只能检测到0~50摄氏度的温度且温度误差在正负2摄氏度内，检测到的湿度范围为20%~90%，且湿度误差在正负5% 范围内。

## 2.7 定时器数据格式介绍

数据名称 | 成员 | 成员介绍 | 权 限 | 占用内存 | 参数介绍
定时器工作 模式 | - | - | 只 读 | 1 Byte | -
- | - | - | - | - | TIMER_SLEEP_MODE（定时器休眠模式） = 0x00
- | - | - | - | - | TIMER_DOWNCNT_MODE（定时器倒计时运 行模式） = 0x01
- | - | - | - | - | TIMER_PERIOD_MODE（定时器时间段运行 模式） = 0x02
- | - | - | - | - | TIMER_CIRCUL_MODE（定时器重复运行模 式） = 0x03
自定义工作 参数 | - | - | 读/ 写 | 1 Byte | 配置定时器自定义运行模式的工作参数
- | 保留 | 保留 | 保 留 | Bit 0(占用该字节 的第0位) | 0~1
- | monday | 周一工作状态 | 读/ | Bit 1(占用该字节 | 0~1

- | monday | 周一工作状态 | 写 | 的第1位) | 0~1
- | tuesday | 周二工作状态 | 读/ 写 | Bit 2(占用该字节 的第2位) | 0~1
- | wednesday | 周三工作状态 | 读/ 写 | Bit 3(占用该字节 的第3位) | 0~1
- | thursday | 周四工作状态 | 读/ 写 | Bit 4(占用该字节 的第4位) | 0~1
- | friday | 周五工作状态 | 读/ 写 | Bit 5(占用该字节 的第5位) | 0~1
- | saturday | 周六工作状态 | 读/ 写 | Bit 6(占用该字节 的第6位) | 0~1
- | sunday | 周日工作状态 | 读/ 写 | Bit 7(占用该字节 的第7位) | 0~1
定时器工作 时间 | - | - | 读/ 写 | 4 Byte | 配置定时器的启动时间和停止时间
- | Start_Hour | 启动时间-小时 | 读/ 写 | 1 Byte | 0~23
- | Start_Minute | 启动时间-分钟 | 读/ 写 | 1 Byte | 0~59
- | Stop_Hour | 启动时间-小时 | 读/ 写 | 1 Byte | 0~23
- | Stop_Minute | 停止时间-分钟 | 读/ 写 | 1 Byte | 0~59
设备控制状 态 | - | - | 读/ 写 | 2 Byte | 配置定时器启动、停止时的设备状态
- device_start_status | | 设备在定时器启动 时的状态 | 读/ 写 | 1 Byte | 根据设备而定
- device_end_status | | 设备在定时器停止 时的状态 | 读/ 写 | 1 Byte | 根据设备而定

### 2.7.1 倒计时模式参数配置

例：倒计时8小时35分钟后关闭

Timer_Mode = TIMER_DOWNCNT_MODE; Start_Hour = Now_Time_Hour; Start_Minute = Now_Time_Minute; Stop_Hour = 8;
Start_Minute = 35;
device_start_status = now_status; device_end_status = off_status;

注：

### 1. 当设定定时器工作在倒计时模式时，定时器工作一次，不会重复运行。 2. 定时器工作在倒计时模式时不允许出现倒计时时间大于24小时的情况，请注意检查。

### 2.7.2 时间段模式参数配置

例：8:50~9:45开启

Timer_Mode = TIMER_SIGNAL_MODE; Start_Hour = 8;
Start_Minute = 50;
Stop_Hour = 9;
Start_Minute = 45;
device_start_status = start_status; device_end_status = end_status;

注：

### 1. 当设定定时器工作在时间段模式时，定时器工作一次，不会重复运行。 2. 定时器工作在时间段模式时不允许出现启动时间大于停止时间的情况，请注意检查。

### 2.7.3 重复运行模式参数配置

例：每周一、周二、周三8:50~9:45开启

Timer_Mode = TIMER_CUSTOM_MODE; monday = 1;
tuesday = 1;
wednesday = 1;
Start_Hour = 8;
Start_Minute = 50;
Stop_Hour = 9;
Start_Minute = 45;
device_start_status = start_status; device_end_status = end_status;

注：

### 1. 当设定定时器工作在重复运行模式时，定时器会重复运行。 2. 定时器工作在重复运行模式时不允许出现启动时间大于停止时间的情况，请注意检查。

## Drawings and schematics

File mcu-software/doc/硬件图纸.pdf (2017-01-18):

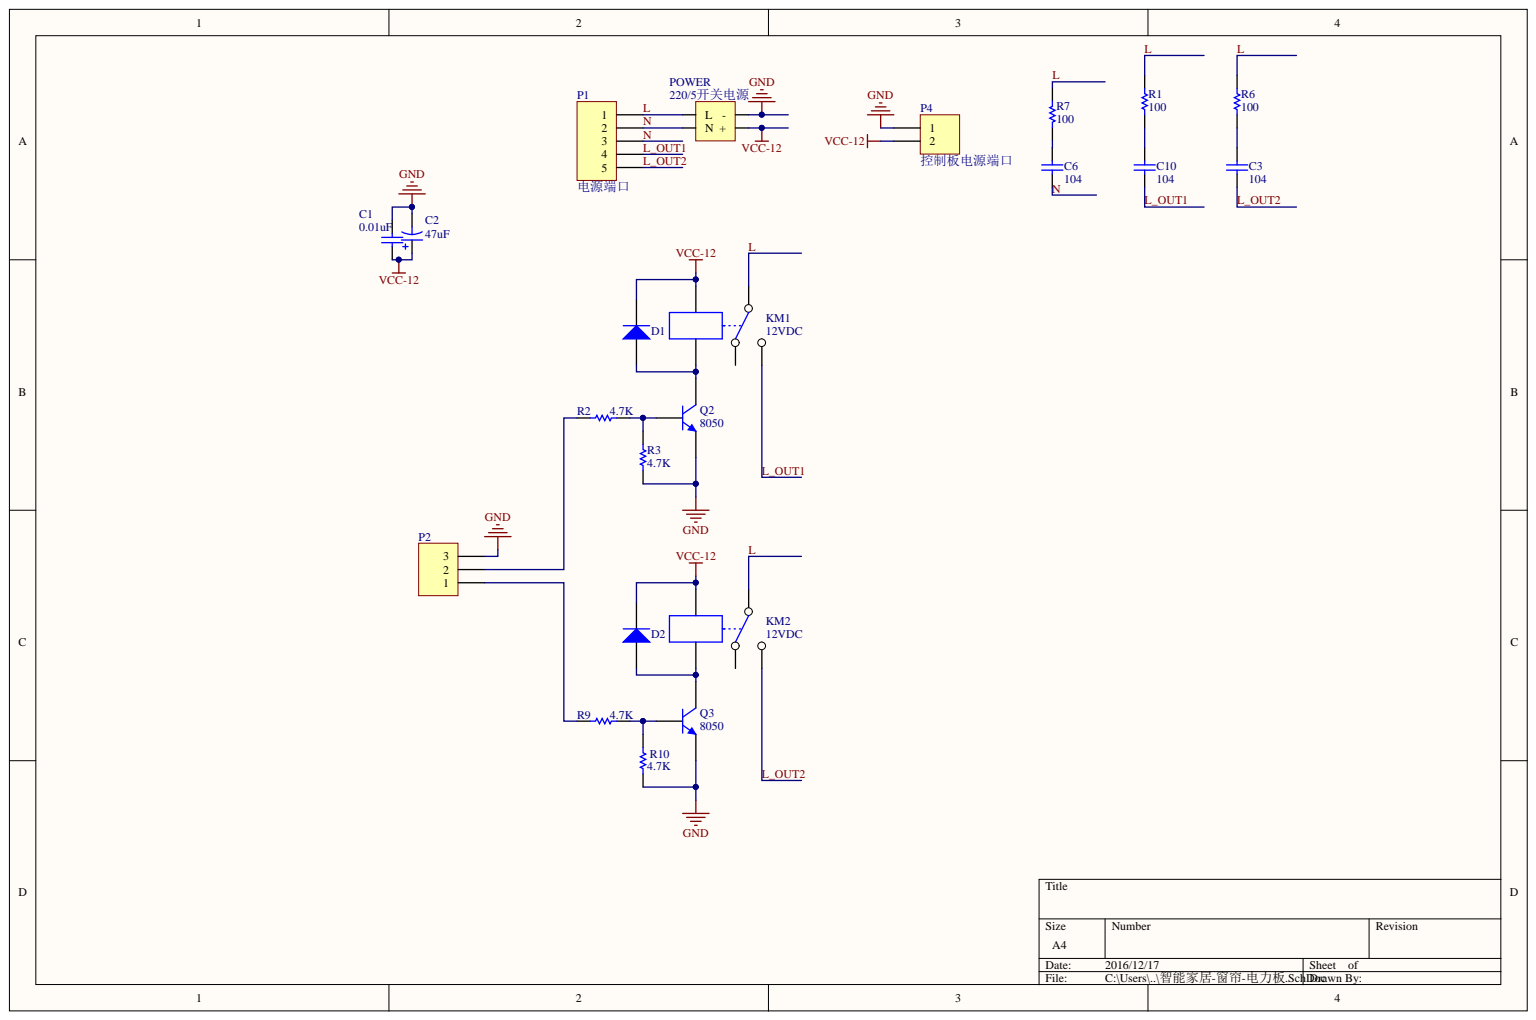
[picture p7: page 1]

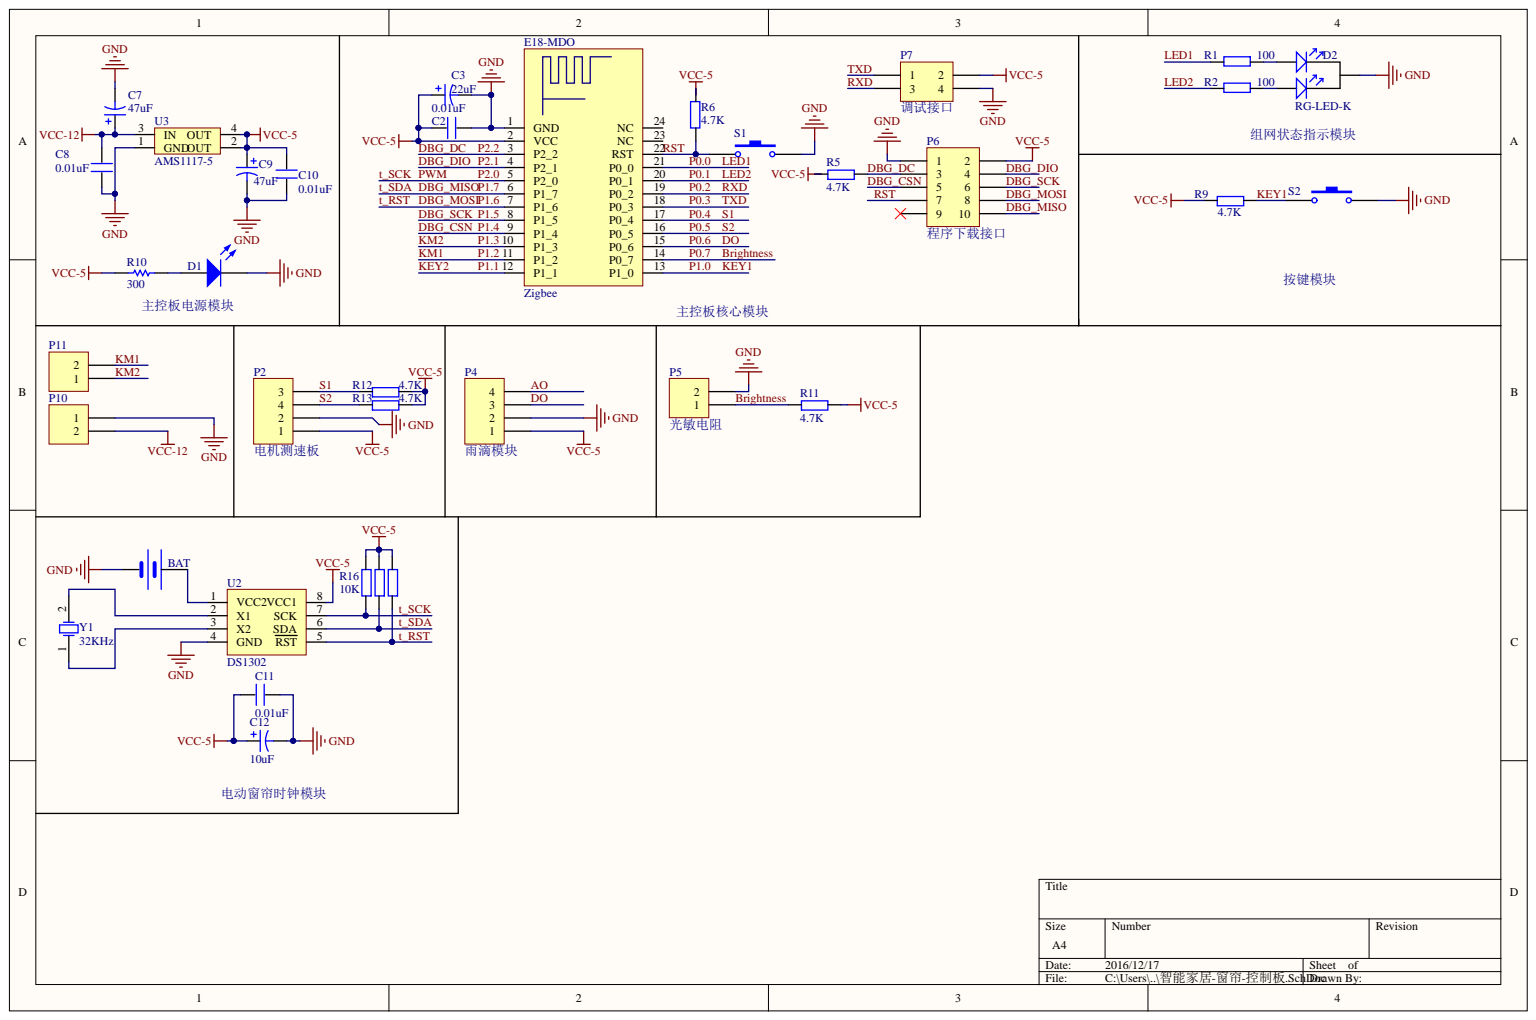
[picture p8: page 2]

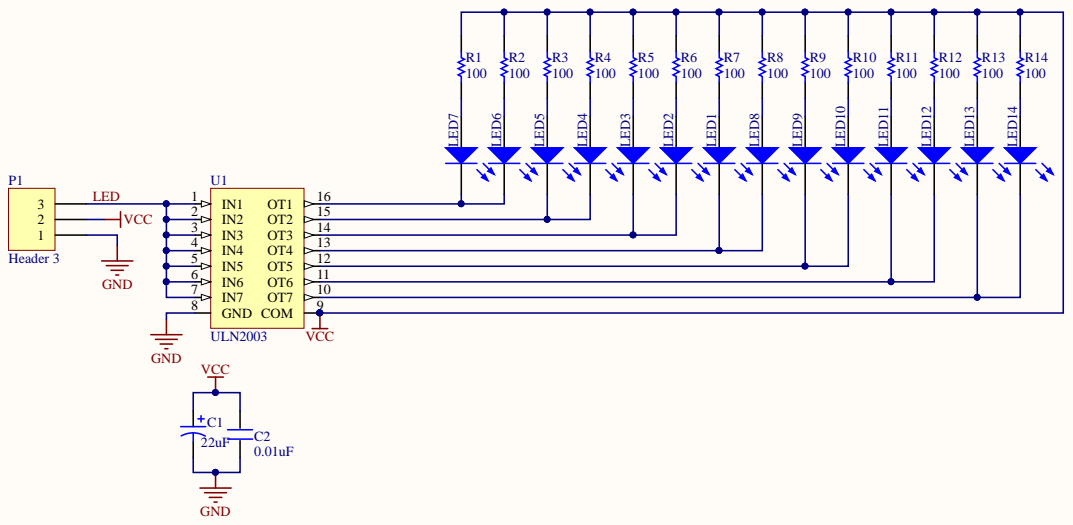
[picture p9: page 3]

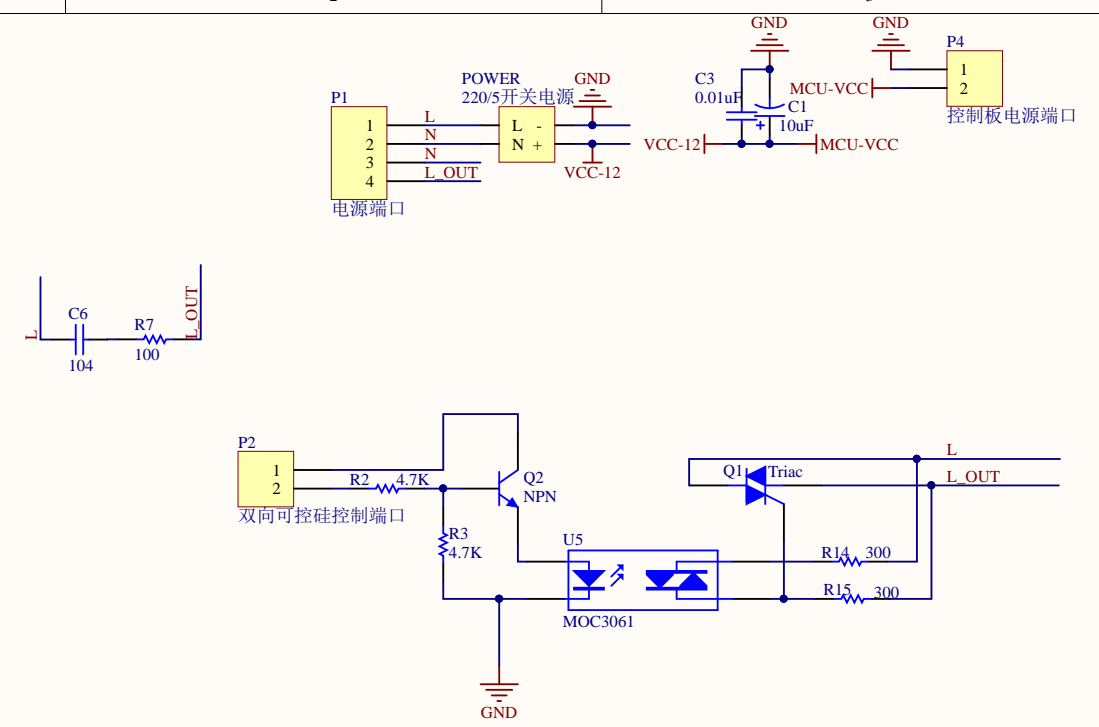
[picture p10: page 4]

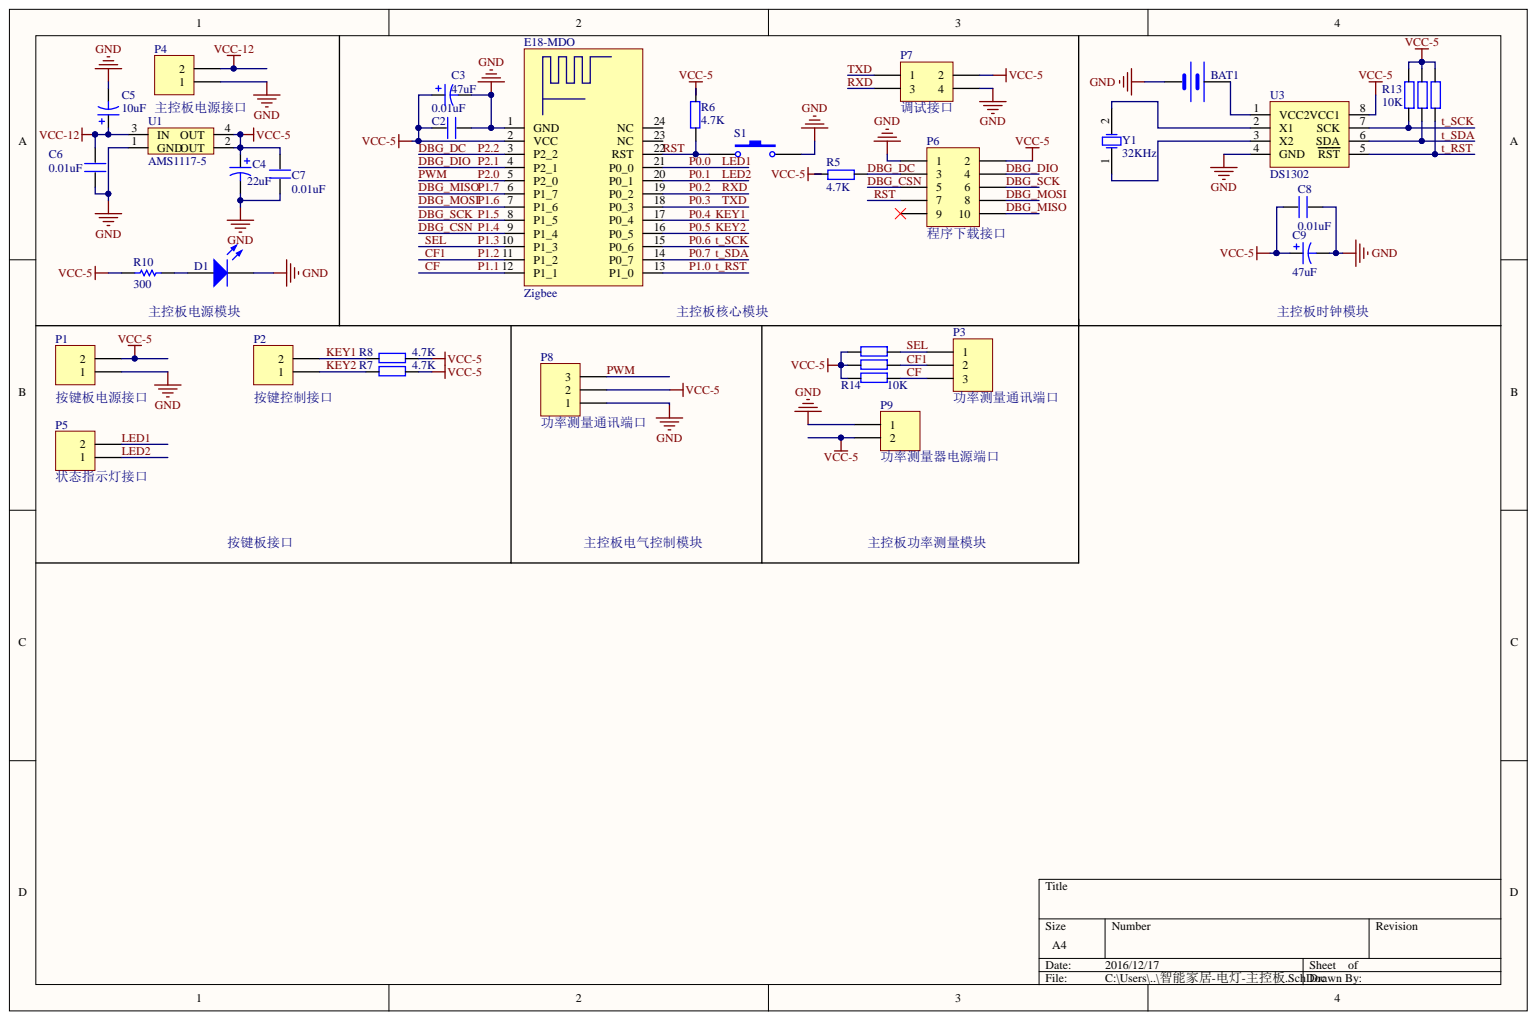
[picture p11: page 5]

GND P4 VCC-12 | E18-MDO

GND 1

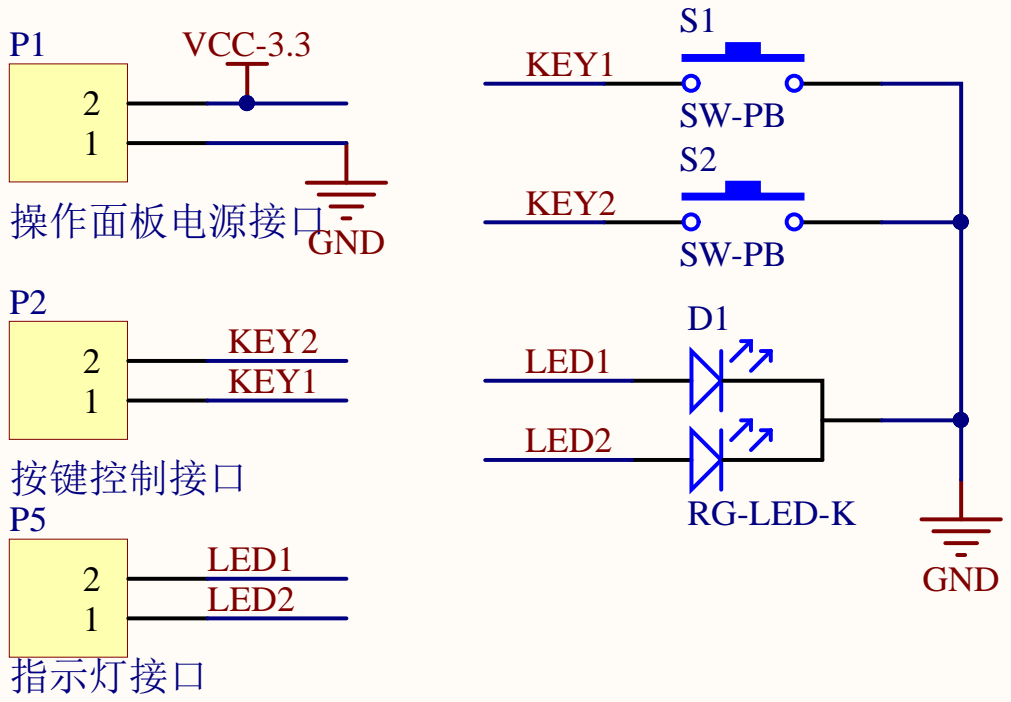
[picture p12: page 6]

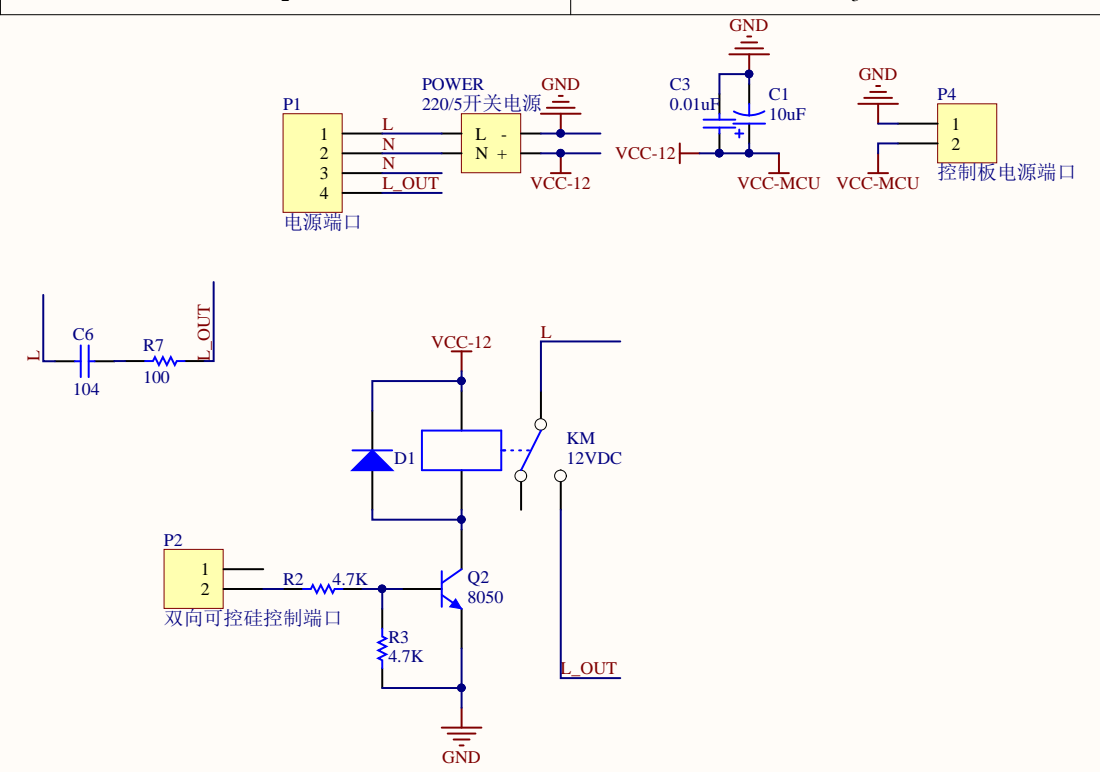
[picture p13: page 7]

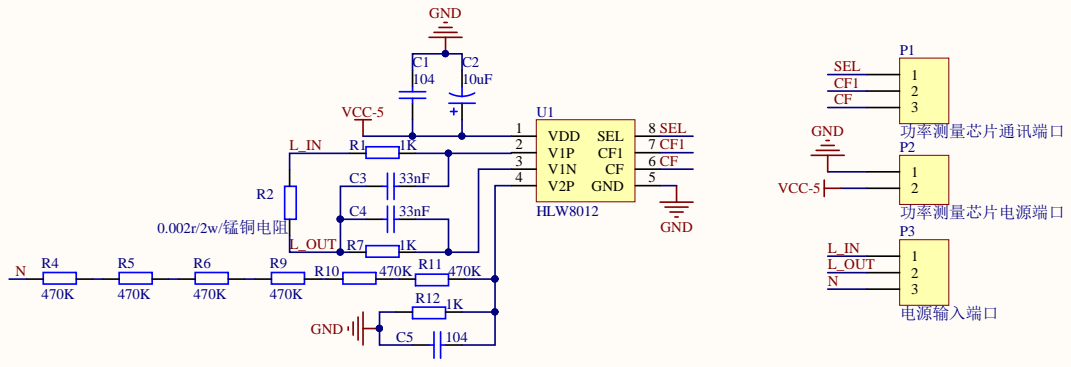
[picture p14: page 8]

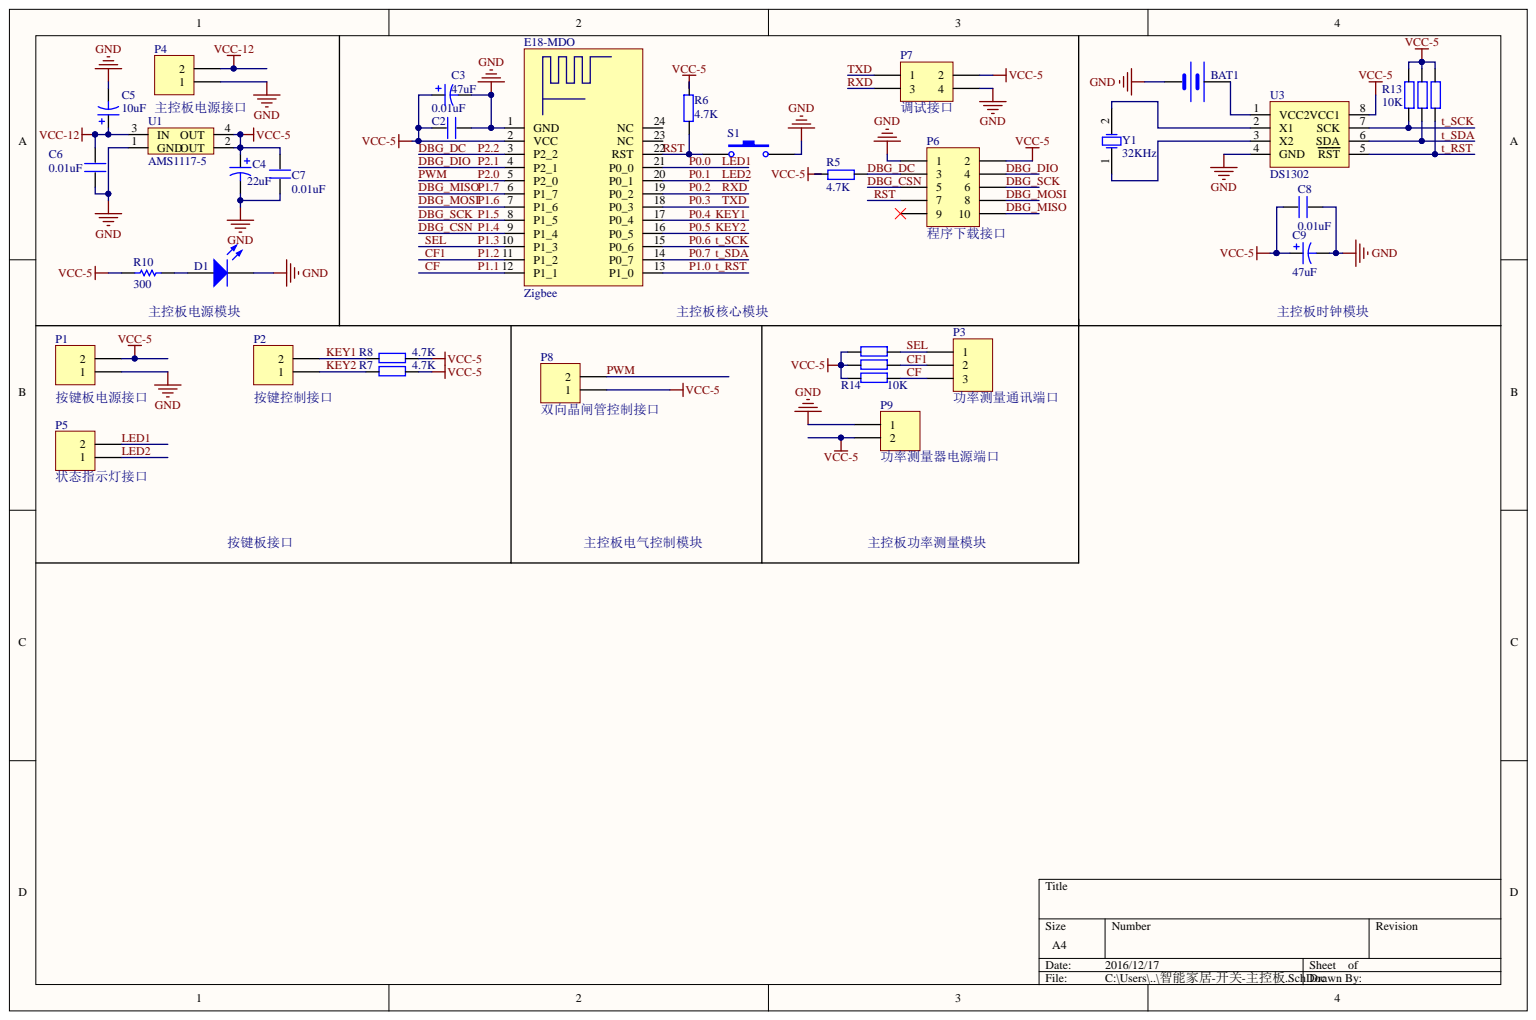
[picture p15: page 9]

GND P4 VCC-12 | E18-MDO

GND 1

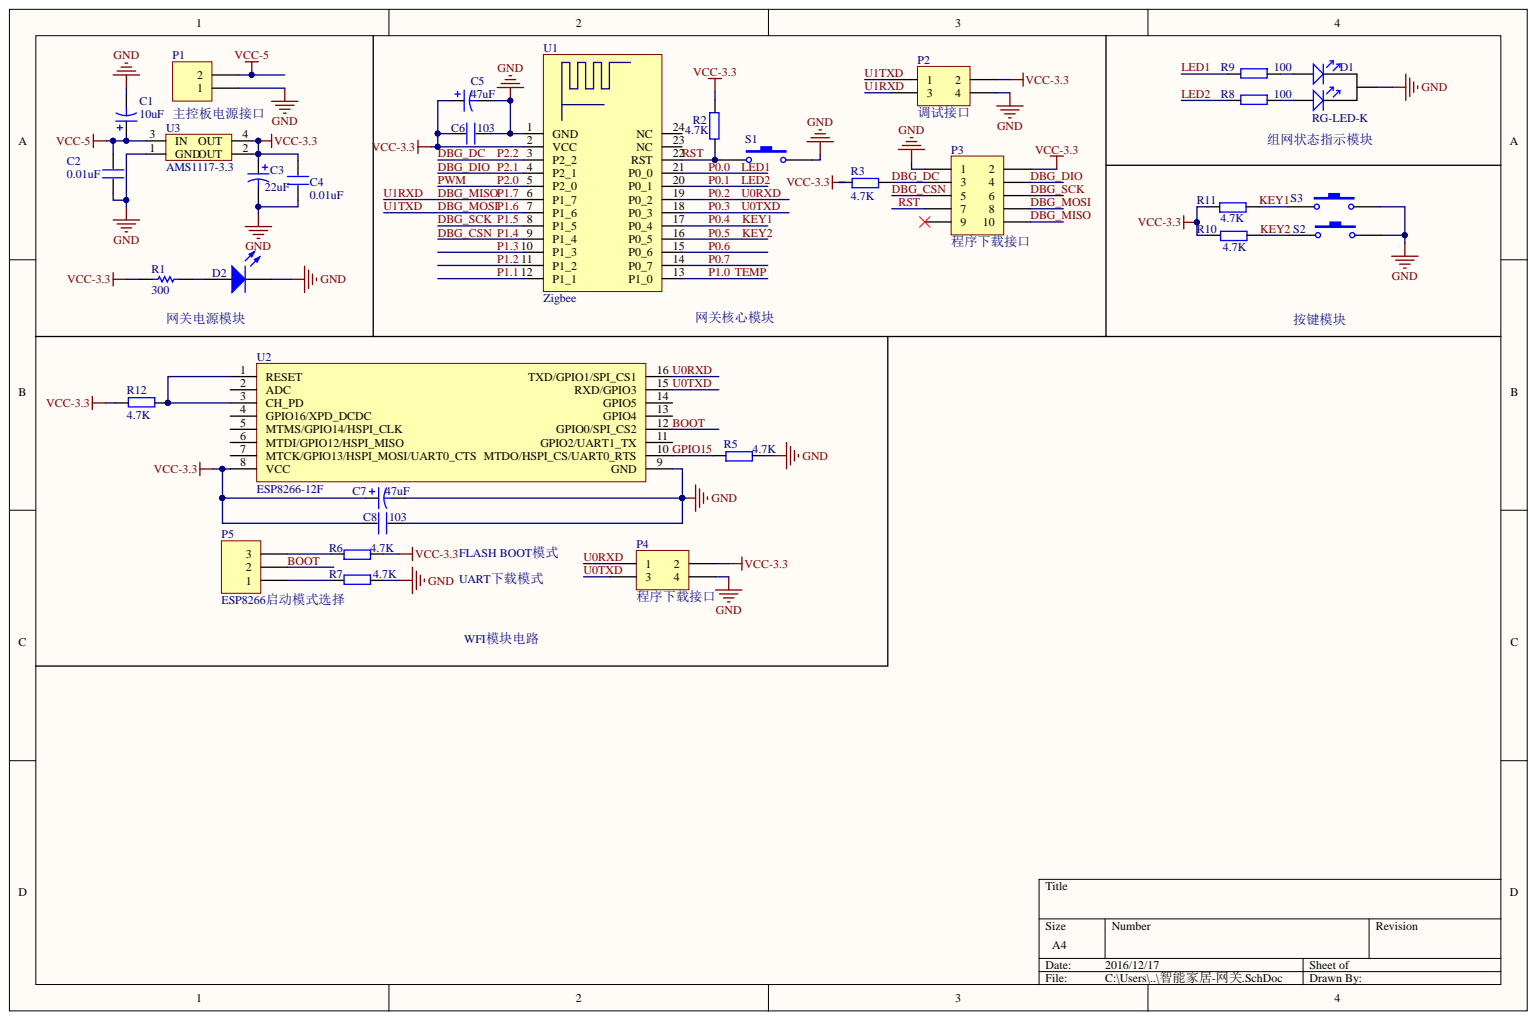
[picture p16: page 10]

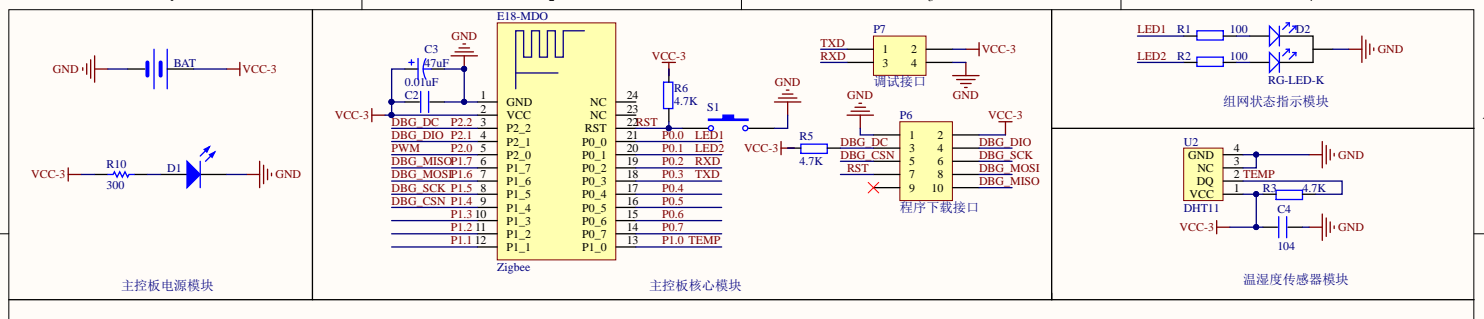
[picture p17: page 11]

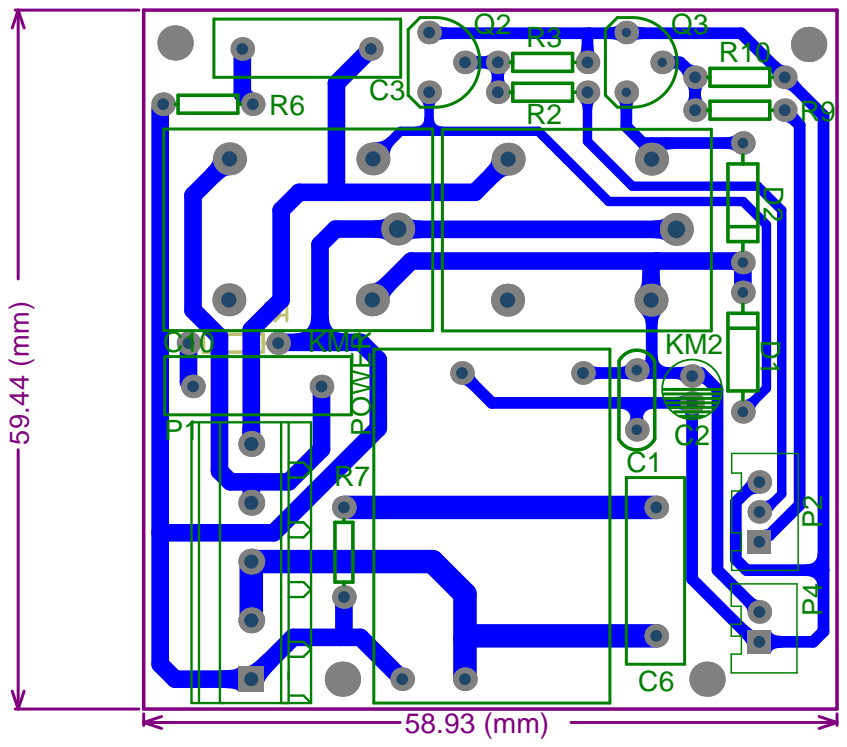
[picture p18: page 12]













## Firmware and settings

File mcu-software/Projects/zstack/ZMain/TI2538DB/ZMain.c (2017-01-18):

/******************************************************************************
  Filename:       ZMain.c
  Revised:        $Date: 2014-09-09 11:13:28 -0700 (Tue, 09 Sep 2014) $
  Revision:       $Revision: 40065 $

  Description:    Startup and task processing code for Z-Stack
  Notes:          This version targets the Texas Instruments CC2538


  Copyright 2012-2013 Texas Instruments Incorporated. All rights reserved.

  IMPORTANT: Your use of this Software is limited to those specific rights
  granted under the terms of a software license agreement between the user
  who downloaded the software, his/her employer (which must be your employer)
  and Texas Instruments Incorporated (the "License"). You may not use this
  Software unless you agree to abide by the terms of the License. The License
  limits your use, and you acknowledge, that the Software may not be modified,
  copied or distributed unless embedded on a Texas Instruments microcontroller
  or used solely and exclusively in conjunction with a Texas Instruments radio
  frequency transceiver, which is integrated into your product. Other than for
  the foregoing purpose, you may not use, reproduce, copy, prepare derivative
  works of, modify, distribute, perform, display or sell this Software and/or
  its documentation for any purpose.

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
  Should you have any questions regarding your right to use this Software,
  contact Texas Instruments Incorporated at www.TI.com.
******************************************************************************/

/******************************************************************************
 * INCLUDES
 */

#include "ZComDef.h"
#include "OSAL.h"
#include "OSAL_Nv.h"
#include "OnBoard.h"
#include "ZMAC.h"

#ifndef NONWK
  #include "AF.h"
#endif

/* Hal */
#include "hal_drivers.h"
#include "hal_lcd.h"
#include "hal_systick.h"

#if defined ( ZCL_KEY_ESTABLISH )
#include "eccapi_163.h"
#include "eccapi_283.h"
#endif

/******************************************************************************
 * LOCAL DEFINITIONS
 */

// TI IEEE Organizational Unique Identifier
#define IEEE_OUI 0x00124B

/******************************************************************************
 * LOCAL FUNCTIONS
 */

static void zmain_dev_info( void );
static void zmain_ext_addr( void );

#if defined ZCL_KEY_ESTABLISH
static void zmain_cert_init( void );
#endif

#ifdef LCD_SUPPORTED
static void zmain_lcd_init( void );
#endif

/******************************************************************************
 * @fn      main
 *
 * @brief   First function called after startup.
 *
 * @param   None
 *
 * @return  Don't care
 */
int main( void )
{
  // Turn off interrupts
  osal_int_disable( INTS_ALL );

  // Initialization for board related stuff such as LEDs
  HAL_BOARD_INIT();

  // Initialize board I/O
  InitBoard( OB_COLD );

  // Initialze HAL drivers
  HalDriverInit();

  // Initialize NV System
  osal_nv_init( NULL );

  // Initialize the MAC
  ZMacInit();

  // Determine the extended address
  zmain_ext_addr();

#if defined ZCL_KEY_ESTABLISH
  // Initialize the Certicom certificate information.
  zmain_cert_init();
#endif

  // Initialize basic NV items
  zgInit();

#ifndef NONWK
  // Since the AF isn't a task, call it's initialization routine
  afInit();
#endif

  // Initialize the operating system
  osal_init_system();

  // Allow interrupts
  osal_int_enable( INTS_ALL );

  SysTickSetup();
  
  // Final board initialization
  InitBoard( OB_READY );

  /* Display the device info on the LCD */
#ifdef LCD_SUPPORTED
  zmain_dev_info();
  zmain_lcd_init();
#endif

#ifdef WDT_IN_PM1
  /* If WDT is used, this is a good place to enable it. */
  WatchDogEnable( WDTIMX );
#endif

  osal_start_system(); // No Return from here

  return 0;  // Shouldn't get here.
} // main()

/******************************************************************************
 * @fn      zmain_ext_addr
 *
 * @brief   Execute a prioritized search for a valid extended address and write
 *          the results into the OSAL NV memory. Temporary IEEE address is not
 *          saved to NV.
 *
 * @param   none
 *
 * @return  none
 */
static void zmain_ext_addr( void )
{
  uint8 nullAddr[Z_EXTADDR_LEN] = {0xFF, 0xFF, 0xFF, 0xFF, 0xFF, 0xFF, 0xFF, 0xFF};
  uint8 writeNV = TRUE;

  // First check whether a non-erased extended address exists in the OSAL NV.
  if ((SUCCESS != osal_nv_item_init(ZCD_NV_EXTADDR, Z_EXTADDR_LEN, NULL))  ||
      (SUCCESS != osal_nv_read(ZCD_NV_EXTADDR, 0, Z_EXTADDR_LEN, aExtendedAddress)) ||
      (osal_memcmp(aExtendedAddress, nullAddr, Z_EXTADDR_LEN)))
  {
    // Attempt to read the extended address from the location in the last flash
    // page where the commissioning tools know to reserve it.
    if (!osal_memcmp((uint8 *)HAL_FLASH_IEEE_ADDR, nullAddr, Z_EXTADDR_LEN))
    {
      (void)osal_memcpy(aExtendedAddress, (uint8 *)HAL_FLASH_IEEE_ADDR, Z_EXTADDR_LEN);
    }
    else
    {
      // Disable prefetch when reading from Information Page.
      uint32 fctl = HWREG(FLASH_CTRL_FCTL);
      HWREG(FLASH_CTRL_FCTL) = fctl & ~(FLASH_CTRL_FCTL_PREFETCH_ENABLE);

      // Copy 64-bit extended address from the Information Page
      (void)osal_memcpy(aExtendedAddress, (uint8*)HAL_INFO_IEEE_ADDR, Z_EXTADDR_LEN);
      if (!osal_memcmp(aExtendedAddress, nullAddr, Z_EXTADDR_LEN))
      {
        uint32 oui = IEEE_OUI;
        // IEEE OUI is located in the upper 3 bytes of an 8-byte extended address
        // Early Test CC2538EMs had the TI OUI located in the 2nd word,
        // Production CC2538 devices have the TI OUI located in the 1st word
        if (osal_memcmp(&aExtendedAddress[1], &oui, 3))
        {
          // OUI found in 1st word, swap words to place OUI in upper bytes
          (void)osal_memcpy(aExtendedAddress, &aExtendedAddress[4], Z_EXTADDR_LEN/2);
          (void)osal_memcpy(&aExtendedAddress[4], (uint8*)HAL_INFO_IEEE_ADDR, Z_EXTADDR_LEN/2);
        }
      }
      else  // No valid extended address was found.
      {
        uint8 idx;

#if !defined ( NV_RESTORE )
        writeNV = FALSE;  // Make a temporary IEEE address, not saved in NV
#endif

       /* Create a sufficiently random extended address for expediency.
        * Note: this is only valid/legal in a test environment and
        *       must never be used for a commercial product.
        */
        for (idx = 0; idx < (Z_EXTADDR_LEN - 2);)
        {
          uint16 randy = osal_rand();
          aExtendedAddress[idx++] = LO_UINT16(randy);
          aExtendedAddress[idx++] = HI_UINT16(randy);
        }
        // Next-to-MSB identifies ZigBee device type.
#if ZG_BUILD_COORDINATOR_TYPE && !ZG_BUILD_JOINING_TYPE
        aExtendedAddress[idx++] = 0x10;
#elif ZG_BUILD_RTRONLY_TYPE
        aExtendedAddress[idx++] = 0x20;
#else
      aExtendedAddress[idx++] = 0x30;
#endif
      // MSB has historical signficance.
        aExtendedAddress[idx] = 0xF8;
      }

      // Restore flash control to previous state
      HWREG(FLASH_CTRL_FCTL) = fctl;
    }

    if (writeNV)
    {
      (void)osal_nv_write(ZCD_NV_EXTADDR, 0, Z_EXTADDR_LEN, aExtendedAddress);
    }
  }

  // Set the MAC PIB extended address according to results from above.
  (void)ZMacSetReq(MAC_EXTENDED_ADDRESS, aExtendedAddress);
}

#if defined ZCL_KEY_ESTABLISH
/******************************************************************************
 * @fn      zmain_cert_init
 *
 * @brief   Initialize the Certicom certificate information.
 *
 * @param   none
 *
 * @return  none
 */
static void zmain_cert_init( void )
{
  uint8 certData[ECCAPI_CERT_283_LEN];
  uint8 nullData[ECCAPI_PUBLIC_KEY_163_LEN] = {
    0xFF, 0xFF, 0xFF, 0xFF, 0xFF, 0xFF, 0xFF, 0xFF,
    0xFF, 0xFF, 0xFF, 0xFF, 0xFF, 0xFF, 0xFF, 0xFF,
    0xFF, 0xFF, 0xFF, 0xFF, 0xFF, 0xFF
  };

  (void)osal_nv_item_init(ZCD_NV_IMPLICIT_CERTIFICATE, ECCAPI_CERT_163_LEN, NULL);
  (void)osal_nv_item_init(ZCD_NV_DEVICE_PRIVATE_KEY, ECCAPI_PRIVATE_KEY_163_LEN, NULL);
  (void)osal_nv_item_init(ZCD_NV_CERT_283, ECCAPI_CERT_283_LEN, NULL);
  (void)osal_nv_item_init(ZCD_NV_PRIVATE_KEY_283, ECCAPI_PRIVATE_KEY_283_LEN, NULL);
  (void)osal_nv_item_init(ZCD_NV_PUBLIC_KEY_283, ECCAPI_PUBLIC_KEY_283_LEN, NULL);

  // First, check whether non-null certificate data already exists in the OSAL NV.
  // To save on code space, just use the CA_PUBLIC_KEY as the bellwether for all three.
  if ((SUCCESS != osal_nv_item_init(ZCD_NV_CA_PUBLIC_KEY, ECCAPI_PUBLIC_KEY_163_LEN, NULL))   ||
      (SUCCESS != osal_nv_read(ZCD_NV_CA_PUBLIC_KEY, 0, ECCAPI_PUBLIC_KEY_163_LEN, certData)) ||
      (osal_memcmp(certData, nullData, ECCAPI_PUBLIC_KEY_163_LEN)))
  {
    // If the certificate data is not NULL, use it to update the corresponding NV items.
    if (!osal_memcmp((uint8 *)HAL_FLASH_CA_PUBLIC_KEY_ADDR, nullData, ECCAPI_PUBLIC_KEY_163_LEN))
    {
      (void)osal_memcpy(certData, (uint8 *)HAL_FLASH_CA_PUBLIC_KEY_ADDR, ECCAPI_PUBLIC_KEY_163_LEN);
      (void)osal_nv_write(ZCD_NV_CA_PUBLIC_KEY, 0, ECCAPI_PUBLIC_KEY_163_LEN, certData);

      (void)osal_memcpy(certData, (uint8 *)HAL_FLASH_IMPLICIT_CERT_ADDR, ECCAPI_CERT_163_LEN);
      (void)osal_nv_write(ZCD_NV_IMPLICIT_CERTIFICATE, 0, ECCAPI_CERT_163_LEN, certData);

      (void)osal_memcpy(certData, (uint8 *)HAL_FLASH_DEV_PRIVATE_KEY_ADDR, ECCAPI_PRIVATE_KEY_163_LEN);
      (void)osal_nv_write(ZCD_NV_DEVICE_PRIVATE_KEY, 0, ECCAPI_PRIVATE_KEY_163_LEN, certData);

      (void)osal_memcpy(certData, (uint8 *)HAL_FLASH_CA_PUBLIC_KEY_283_ADDR, ECCAPI_PUBLIC_KEY_283_LEN);
      (void)osal_nv_write(ZCD_NV_PUBLIC_KEY_283, 0, ECCAPI_PUBLIC_KEY_283_LEN, certData);

      (void)osal_memcpy(certData, (uint8 *)HAL_FLASH_IMPLICIT_CERT_283_ADDR, ECCAPI_CERT_283_LEN);
      (void)osal_nv_write(ZCD_NV_CERT_283, 0, ECCAPI_CERT_283_LEN, certData);

      (void)osal_memcpy(certData, (uint8 *)HAL_FLASH_DEV_PRIVATE_KEY_283_ADDR, ECCAPI_PRIVATE_KEY_283_LEN);
      (void)osal_nv_write(ZCD_NV_PRIVATE_KEY_283, 0, ECCAPI_PRIVATE_KEY_283_LEN, certData);
    }
  }
}
#endif

#ifdef LCD_SUPPORTED
/******************************************************************************
 * @fn      zmain_dev_info
 *
 * @brief   Displays the IEEE address (MSB to LSB) on the LCD.
 *
 * @param   none
 *
 * @return  none
 */
static void zmain_dev_info( void )
{
  uint8 i;
  uint8 *xad;
  uint8 lcd_buf[(Z_EXTADDR_LEN*2)+1];

  // Display the extended address.
  xad = aExtendedAddress + Z_EXTADDR_LEN - 1;

  for (i = 0; i < Z_EXTADDR_LEN*2; xad--)
  {
    uint8 ch;
    ch = (*xad >> 4) & 0x0F;
    lcd_buf[i++] = ch + (( ch < 10 ) ? '0' : '7');
    ch = *xad & 0x0F;
    lcd_buf[i++] = ch + (( ch < 10 ) ? '0' : '7');
  }
  lcd_buf[Z_EXTADDR_LEN*2] = '\0';
  HalLcdWriteString( "IEEE: ", HAL_LCD_LINE_2 );
  HalLcdWriteString( (char*)lcd_buf, HAL_LCD_LINE_3 );
}
#endif

#ifdef LCD_SUPPORTED
/*********************************************************************
 * @fn      zmain_lcd_init
 * @brief   Initialize LCD at start up.
 * @return  none
 *********************************************************************/
static void zmain_lcd_init( void )
{
#ifdef SERIAL_DEBUG_SUPPORTED
  {
    HalLcdWriteString( "TexasInstruments", HAL_LCD_LINE_1 );

#if defined( MT_MAC_FUNC )
#if defined( ZDO_COORDINATOR )
      HalLcdWriteString( "MAC-MT Coord", HAL_LCD_LINE_2 );
#else
      HalLcdWriteString( "MAC-MT Device", HAL_LCD_LINE_2 );
#endif // ZDO
#elif defined( MT_NWK_FUNC )
#if defined( ZDO_COORDINATOR )
      HalLcdWriteString( "NWK Coordinator", HAL_LCD_LINE_2 );
#else
      HalLcdWriteString( "NWK Device", HAL_LCD_LINE_2 );
#endif // ZDO
#endif // MT_FUNC
  }
#endif // SERIAL_DEBUG_SUPPORTED
}
#endif

/******************************************************************************
 */

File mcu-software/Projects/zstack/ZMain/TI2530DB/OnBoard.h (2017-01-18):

/**************************************************************************************************
  Filename:       OnBoard.h
  Revised:        $Date: 2012-03-29 12:09:02 -0700 (Thu, 29 Mar 2012) $
  Revision:       $Revision: 29943 $

  Description:    Defines stuff for EVALuation boards
  Notes:          This file targets the Chipcon CC2530/31


  Copyright 2005-2010 Texas Instruments Incorporated. All rights reserved.

  IMPORTANT: Your use of this Software is limited to those specific rights
  granted under the terms of a software license agreement between the user
  who downloaded the software, his/her employer (which must be your employer)
  and Texas Instruments Incorporated (the "License").  You may not use this
  Software unless you agree to abide by the terms of the License. The License
  limits your use, and you acknowledge, that the Software may not be modified,
  copied or distributed unless embedded on a Texas Instruments microcontroller
  or used solely and exclusively in conjunction with a Texas Instruments radio
  frequency transceiver, which is integrated into your product.  Other than for
  the foregoing purpose, you may not use, reproduce, copy, prepare derivative
  works of, modify, distribute, perform, display or sell this Software and/or
  its documentation for any purpose.

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
  Should you have any questions regarding your right to use this Software,
  contact Texas Instruments Incorporated at www.TI.com.
**************************************************************************************************/

#ifndef ONBOARD_H
#define ONBOARD_H

#ifdef __cplusplus
extern "C"
{
#endif

/*********************************************************************
 * INCLUDES
 */

#include "hal_mcu.h"
#include "hal_uart.h"
#include "hal_sleep.h"
#include "osal.h"

/*********************************************************************
 * GLOBAL VARIABLES
 */

// 64-bit Extended Address of this device
extern uint8 aExtendedAddress[8];

/*********************************************************************
 * CONSTANTS
 */

// Timer clock and power-saving definitions
#define TIMER_DECR_TIME    1  // 1ms - has to be matched with TC_OCC

/* OSAL timer defines */
#define TICK_TIME   1000   // Timer per tick - in micro-sec
/*
  Timer4 interrupts @ 1.0 msecs using 1/128 pre-scaler
  TICK_COUNT = (CPUMHZ / 128) / 1000
*/
#define TICK_COUNT  1  // 32 Mhz Output Compare Count

/* CC2430 DEFINITIONS */

// MEMCTR bit definitions
#define ALWAYS1    0x01  // Reserved: always=1
#define CACHDIS    0x02  // Flash cache: disable=1
#define FMAP0      0x10  // Flash bank map, bit0
#define FMAP1      0x20  // Flash bank map, bit1
#define FMAP       0x30  // Flash bank map, mask
#define MUNIF      0x40  // Memory mapping: unified=1

// PCON bit definitions
#define PMODESET   0x01  // Power mode control: 1=set PMx

// Reset bit definitions
#define LRESET     0x18  // Last reset bit mask
#define RESETPO    0x00  // Power-On reset
#define RESETEX    0x08  // External reset
#define RESETWD    0x10  // WatchDog reset

/* GPIO PORT DEFINITIONS */
// GPIO bit definitions
#define GPIO_0     0x01  // Px_0: GPIO=0, PIO=1
#define GPIO_1     0x02  // Px_1: GPIO=0, PIO=1
#define GPIO_2     0x04  // Px_2: GPIO=0, PIO=1
#define GPIO_3     0x08  // Px_3: GPIO=0, PIO=1
#define GPIO_4     0x10  // Px_4: GPIO=0, PIO=1
#define GPIO_5     0x20  // Px_5: GPIO=0, PIO=1
#define GPIO_6     0x40  // Px_6: GPIO=0, PIO=1
#define GPIO_7     0x80  // Px_7: GPIO=0, PIO=1

/* WATCHDOG TIMER DEFINITIONS */
// WDCTL bit definitions

#define WDINT0     0x01  // Interval, bit0
#define WDINT1     0x02  // Interval, bit1
#define WDINT      0x03  // Interval, mask
#define WDMODE     0x04  // Mode: watchdog=0, timer=1
#define WDEN       0x08  // Timer: disabled=0, enabled=1
#define WDCLR0     0x10  // Clear timer, bit0
#define WDCLR1     0x20  // Clear timer, bit1
#define WDCLR2     0x40  // Clear timer, bit2
#define WDCLR3     0x80  // Clear timer, bit3
#define WDCLR      0xF0  // Clear timer, mask

// WD timer intervals
#define WDTISH     0x03  // Short: clk * 64
#define WDTIMD     0x02  // Medium: clk * 512
#define WDTILG     0x01  // Long: clk * 8192
#define WDTIMX     0x00  // Maximum: clk * 32768

// WD clear timer patterns
#define WDCLP1     0xA0  // Clear pattern 1
#define WDCLP2     0x50  // Clear pattern 2

/*********************************************************************
 * MACROS
 */

// These Key definitions are unique to this development system.
// They are used to bypass functions when starting up the device.
#define SW_BYPASS_NV    HAL_KEY_SW_5  // Bypass Network layer NV restore
#define SW_BYPASS_START HAL_KEY_SW_1  // Bypass Network initialization

// LCD Support Defintions
#ifdef LCD_SUPPORTED
  #if !defined DEBUG
    #define DEBUG  0
  #endif
  #if LCD_SUPPORTED==DEBUG
 //   #define SERIAL_DEBUG_SUPPORTED  // Serial-debug
  #endif
#else // No LCD support
  #undef SERIAL_DEBUG_SUPPORTED  // No serial-debug
#endif
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

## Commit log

2017-01-18 新建分支
2017-01-18 创建硬件分支
    [ESP8266V1.2.SCHLIB, ESP8266二版.PcbLib, RLC.PcbLib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]
2017-01-18 添加说明
2017-01-18 修改说明文档
2017-01-18 修改开关按键板PCB布局
    [智能家居-开关-按键板(红色电容按键).PcbDoc, 智能家居-开关-按键板(蓝色电容按键).PcbDoc, 智能家居-开关-按键板.PcbDoc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]
2017-01-18 增加窗帘的时钟电路
    [智能家居-开关-主控板.PcbDoc, 智能家居-窗帘.PcbDoc, 智能家居-窗帘.SchDoc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]
2017-01-18 修改电力板驱动电路
    [接插件.PcbLib, 智能家居-开关-电力板.PcbDoc, 智能家居-开关-电力板.SchDoc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]
2017-01-18 取消电力板5v电压输出
    [智能家居-开关-主控板.PcbDoc, 智能家居-开关-主控板.SchDoc, 智能家居-开关-电力板.PcbDoc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]
2017-01-18 修改单片机复位电路
    [智能家居-开关-主控板.PcbDoc, 智能家居-开关-主控板.SchDoc, 智能家居-温湿度传感器.PcbDoc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]
2017-01-18 修改窗帘电力板电路：增加阻容吸收电路
    [ESP8266V1.2.SCHLIB, ESP8266二版.PcbLib, RLC.PcbLib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]
2017-01-18 实现zigbee设备P2P通讯
    [f8wConfig.cfg, f8wCoord.cfg, f8wEndev.cfg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]
2017-01-18 移植机智云固件
2017-01-18 开启双串口，已知问题UART1无法接收发送数据
2017-01-18 双串口通讯收发仍不正常
2017-01-18 UART0实现与ESP8266通讯
2017-01-18 支持应答错误数据
2017-01-18 添加结束通讯应答机制
2017-01-18 完成Gizwits通讯与Zigbee之间的相互兼容测试
2017-01-18 修改机智云固件刷新时间
2017-01-18 数据解析暂未完成
2017-01-18 修复了终端设备串口波特率调整不当的问题
2017-01-18 心跳连接成功
2017-01-18 关闭ZSTACK自带的LED驱动和KEY驱动
2017-01-18 添加定时器驱动函数
2017-01-18 实现呼吸灯例程
2017-01-18 使用定时器3中断更新呼吸灯的数值
2017-01-18 修改定时器驱动库
2017-01-18 Flash操作成功
2017-01-18 移除官方的定时器驱动程序
2017-01-18 支持按键检测
2017-01-18 整合资源模块
2017-01-18 更改程序结构，开始进行重构
2017-01-18 完成数据包发送程序的整合
2017-01-18 进一步整合程序结构
2017-01-18 恢复心跳结构
2017-01-18 添加DHT11、DS1302驱动
2017-01-18 修改DS1302驱动程序、智能灯的初始化程序
2017-01-18 增加应用层操作逻辑
2017-01-18 优化程序层次逻辑
2017-01-18 更改通讯协议部分内容
2017-01-18 完成定时器状工作状态检测函数的编写
2017-01-18 更新定时器类型的数据结构
2017-01-18 修改通讯协议部分内容
2017-01-18 修改通讯协议，完成对定时器任务的处理
2017-01-18 设备类型条件编译出错
2017-01-18 解决设备型号条件编译出错的问题
2017-01-18 修改通讯协议
2017-01-18 修改通讯类型
2017-01-18 修改底层通讯程序
2017-01-18 修改部分通讯协议内容，增加通讯流程说明
2017-01-18 完成智能灯的编程工作，进入DEBUG阶段。
2017-01-18 添加机智云初始化程序
2017-01-18 终端设备无法加入网络
2017-01-18 修复机智云通讯时间计数器未启动的问题
2017-01-18 关闭Z-STACK自带的按键方案，采用自主开发的按键方案
2017-01-18 修复无法处理按键事件的BUG，ZIGBEE组网不正常。
2017-01-18 添加智能电灯定时器后台刷新程序
2017-01-18 修复了DS1302数据读写错误的BUG
2017-01-18 修复了DHT11读取数据时校验和计算错误的BUG
2017-01-18 修改按键检测处理程序
2017-01-18 修改设备状态变化处理，修改通讯协议通讯类型部分，已知BUG：从机发送给主机数据主机接收不到
2017-01-18 修改通讯协议定时器部分注释
2017-01-18 整理MYPROTOCOL
2017-01-18 优化MYPROTOCOL结构
2017-01-18 修正MYPROTOCOL发送目标设设置不正确的BUG
2017-01-18 全面整合MYPROTOCOL模块
2017-01-18 去除MYPROTOCOL的发送缓冲区
2017-01-18 修改数据包发送函数
2017-01-18 P2P连接成功
2017-01-18 去除USE_GIZWITS_MOD宏，改用MYPROTOCOL_DEVICE_COORD宏
2017-01-18 修改MYPROTOCOL的日志打印宏配置
2017-01-18 修复了向数据列表写入数据信息不正确的bug
2017-01-18 修复组网LED显示不正常的BUG(主要表现为终端设备断开网络指示灯依旧显示已连接状态)；已知BUG：若用户上报云端的数据有0xFF会造成APP接收到的数据为空。
2017-01-18 修改通讯协议定时器章节说明
2017-01-18 修改通讯协议介绍
2017-01-18 备份通讯协议
2017-01-18 更新通讯协议定时器章节部分内容
2017-01-18 更新通讯协议定时器章节的说明，修改定时器程序
2017-01-18 目前定时器程序支持目前通讯协议所规定的标准
2017-01-18 添加温湿度传感器、插座程序
2017-01-18 修改温湿度传感器命令
2017-01-18 修复了网关未连接APP仍然向APP发送命令的请求 修改发送温湿度数据发送周期为一分钟
2017-01-18 修改网关回复APP请求控制设备应答
2017-01-18 整合资源
2017-01-18 更新通讯内容
2017-01-18 1. 增加电动窗帘代码 2. 同步通讯程序-智能电灯
2017-01-18 修改功能引脚配置
2017-01-18 修改窗帘按键端口
2017-01-18 修改按键检测策略
2017-01-18 修改串口底层发送程序
2017-01-18 1. 增加帮助文档 2. 增加星期计算函数 3. 增加从云端获取网络时间函数
2017-01-18 1. 修改存储函数 2. 新增窗帘正反转运行驱动 3. 修改按键处理程序 4. 窗帘运行方案待解决 5. 去除一些过时的程序
2017-01-18 1. 更新硬件电路 2. 完善窗帘硬件抽象层 3. 修改DS1302驱动
2017-01-18 1. 添加ADC转换例程 2. 修改定时器配置文件的名称
2017-01-18 修改窗帘模块功能
2017-01-18 增加窗帘应答程序
2017-01-18 添加自动校时程序
2017-01-18 添加插座初始化函数
2017-01-18 修改工程头文件目录
2017-01-18 修复了温湿度数据读取失败的BUG
2017-01-18 降低读取温湿度模块所需的时间
2017-01-18 重写MYPROTOCOL程序框架
2017-01-18 新建模版工程
2017-01-18 采用标准库进行结构体偏移量计算
2017-01-18 修改老式设备类型判断宏
2017-01-18 重写设备列表相关功能函数
2017-01-18 添加COORD设备控制文件
2017-01-18 完成COORD程序的编写
2017-01-18 修改空应答机制
2017-01-18 解决抓包失败导致接收缓冲区错误的Bug
2017-01-18 按键反应迟钝
2017-01-18 提升通讯稳定性
2017-01-18 修正zigbee设备底层通讯错误的BUG
2017-01-18 等待稳定性测试
2017-01-18 已知问题窗帘运行时程序会跑飞
2017-01-18 解决窗帘程序跑飞的问题
2017-01-18 等待DEBUG
2017-01-18 修复设备从网关获取时间不正确的bug 已知问题：设备写入时间到DS1302错误
2017-01-18 修复了读取设备列表不正确的BUG，禁用除COORD设备的串口2驱动
2017-01-18 修改工程清理文件
2017-01-18 修复设备无法上报状态的BUG
2017-01-18 修复倒计时定时器不能正常工作的BUG
2017-01-18 ZSTACK的NV操作调试成功
2017-01-18 + 添加更新日志。 + 添加设备时钟芯片使能/禁用开关。 + 添加设备数据保存使能/禁用开关。 + 修改电灯默认上电状态为关闭状态。
2017-01-18 解决了电动窗帘无法实现远程和按键连续控制的BUG。
2017-01-18 固件版本：IOTBaseOnGizwits_MCUSoftwareDebug_0.2.10_alpha_201612240022 + 修复了电动窗帘上电自动运行的BUG。 + 修复了电动窗帘按键失灵的BUG。 + 修复了按键过于灵敏的BUG。
    [bsp_curtain.c, bsp_key.h, bsp_light.c]
2017-01-18 固件版本：IOTBaseOnGizwits_MCUSoftwareDebug_0.2.11_alpha_201612242230 + 修复了定时器运行错误的BUG。 + 修复了网关获取网络时间过长的BUG。 + 修改网关清除僵尸设备的时间。 + 延长设备心跳时间。 + 添加定时器操作设备的状态上报操作。 + 修复的下雨状态检测不正常的BUG。 + 修复通讯协议部分内容。 + 添加电灯设备的路由分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
    [bsp_curtain.c, bsp_light.c]
2017-01-18 固件版本：IOTBaseOnGizwits_MCUSoftwareDebug_0.2.12_alpha_201612252330 + 修复了窗帘定时器回调存在递归的BUG。 + 修改通讯协议标注错误的问题。
    [bsp_curtain.c]
2017-01-18 固件版本：IOTBaseOnGizwits_MCUSoftwareDebug_0.2.13_alpha_201612252343 + 切换电灯控制按键为电容按键。
2017-01-18 修改窗帘速度检测时间
2017-01-18 固件版本：IOTBaseOnGizwits_MCUSoftwareDebug_0.2.15_alpha_201612261700 + 添加网关获取网络事时间前置标志。
2017-01-18 固件版本：IOTBaseOnGizwits_MCUSoftwareDebug_0.2.16_alpha_201612261448 + 修改网络时间推送策略，改为网关获取到时间更新主动推送给其他设备，设备会在30s内主动获取网络时间。 + 添加发送广播程序。 + 添加写入设备时间命令的解析。
2017-01-18 固件版本：IOTBaseOnGizwits_MCUSoftwareDebug_0.2.17_alpha_201612282310 + 添加检测到新设备就向APP发送请求更新设备列表命令(待测试)。
    [f8wConfig.cfg, f8wCoord.cfg, f8wEndev.cfg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]
2017-01-18 sdk初始 email注册登录 wifi连接
2017-01-18 设备绑定相关
2017-01-18 第一版（基于5.0）
2017-01-18 登录界面UI基本完成
2017-01-18 6.0权限部分,待完善
2017-01-18 已通过连接测试
2017-01-18 登录与注册部分完成重构
2017-01-18 登录加入自动存储,设备列表初成
2017-01-18 设备列表BUG待解决
2017-01-18 设备绑定BUG待解决
2017-01-18 sdk更新,设备列表微调
2017-01-18 主控界面初步成型
2017-01-18 sdk更新 自动登录加入
2017-01-18 界面改，数据库加入
2017-01-18 定时器去除，通信数据更新（收发数据列表，app改灯状态 已测试成功）
2017-01-18 数据集发送全部完成，接收全部完成（待测试）
2017-01-18 收发测试完成
2017-01-18 修复mac地址显示问题
2017-01-18 使用了新的通信协议
2017-01-18 增加了对6.0权限的适配
2017-01-18 界面大改
2017-01-18 bug基本解决。还有设备列表问题待解决
2017-01-18 设备列表问题已解决
2017-01-18 完成所有功能测试
2017-01-18 细节优化
2017-01-18 改变文件结构
2017-01-18 合并代码
